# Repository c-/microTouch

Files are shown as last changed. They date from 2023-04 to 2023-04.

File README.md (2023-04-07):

# microTouch

Compact 3D printer bed probe based (very) loosely on the
[TinyTouch NMPG](https://www.thingiverse.com/thing:4661556).

microTouch In Action

I designed and built the first prototype a couple years ago. The current
version has been running since (approximately) May 2022 and has been
quite reliable, with only one misfire that I can remember.

# Design

It uses the same nano servo and a gravity based deployment as the
TT NMPG just started as a project to build a smaller TT PCB, but I've
changed it up to use a hall effect sensor with a small magnet embedded
in the slider, which allows for an even more compact package. I've also
changed the connector to a PH 2.0 and removed the servo connector
completely, soldering it directly to the PCB.

The size of the PCB is approximately 35mm x 25mm, and the shell will add
another 10mm or so. It should comfortably fit in the space needed by
a BLTouch.

I think there's room to crunch the design down even smaller, but I'm not
sure there's any need for a nanoTouch.

# Bill Of Materials

There's an [Interactive BOM](bom/ibom.html) for the electronics.

 * Nano linear servo (RH only). In theory you could use a LH version, but you'd
need to flip the mirror *everything*, including the hall sensor and magnet.
I haven't tested that.
 * A3144 hall effect sensor. This is an obsolete part, but it's still
available.
 * JST PH 2.0 connector. You can use a four or five pin, depending on
whether you need a different voltage for the signal than what the servo
uses (i.e. servo is 5V, signal might be 3.3V). If you use the 5 pin version
then you'll need to cut the solder jumper on the back.
 * 10uF, 100nF 0805 capacitors
 * 4.7K 0805 resistors
 * 0805 red LED (other colors probably work, but I've only tested red)
 * 3x2mm rare earth magnet

You'll need a PCB. It *can* be homemade (I made the first version on a PCB
mill), but you'll have a battle with the servo pads. I ordered my finished
versions [from Oshpark](https://oshpark.com/shared_projects/54oETibN),
and you can't really beat the price for something that small.

You'll need printed parts. Minimally the slider and the cover, and I found
a backer/spacer necessary, but you might need to design a different way to
mount to your printer.  I printed the slider with
[Igus iglide I150-PF](https://www.igus.com/product/12404),
but probably anything would work okay. The slider and the body need to be
sanded to ensure smooth deployment, and getting that right is by far the
most finicky part of the job. You'll probably have to drill the slider hole
larger to hold the magnet (a press fit is enough).

For the probe itself I use a M3 bolt (25mm, I think?), but anything you can
thread into the slider body should be fine as long as it has some weight to
it. The bolt can be threaded in quite far and is the main way to adjust
the position of the problem, along with the servo angles.

# Assembly

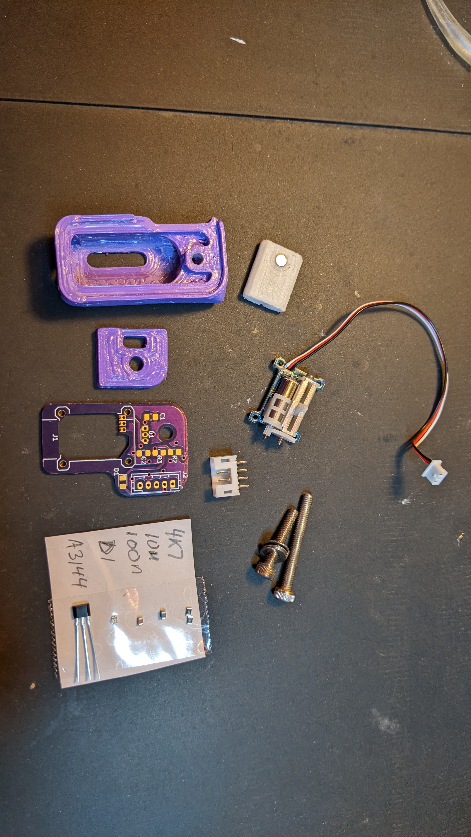
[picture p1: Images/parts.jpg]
All the parts


Remove the wires from the servo.

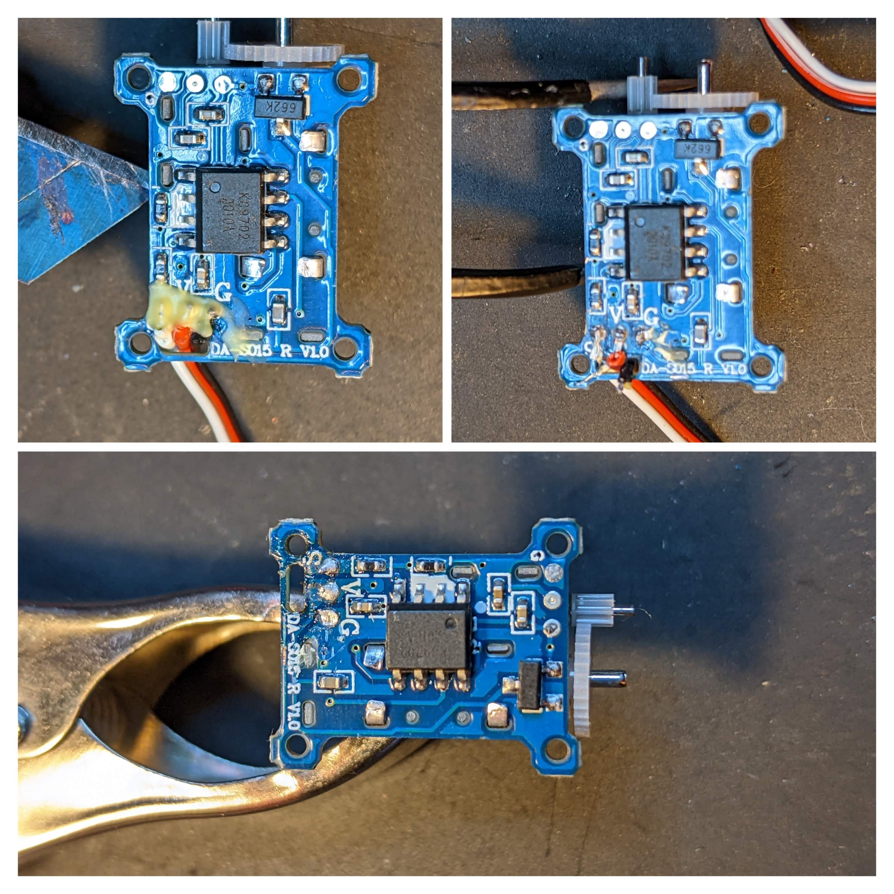
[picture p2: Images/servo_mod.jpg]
Servo wirectomy


Do this by scraping away the glue at the PCB, then desolder the wires and
touch up the pads with fresh solder. Don't overbuild solder on the pads,
they should be somewhat flat.

Solder the components. See the Interactive bom for details of what goes
where. Do the surface mount components first or you'll find things get
cramped. The hall sensor should be mounted a bit off the board, just below
where the slider will clear it.

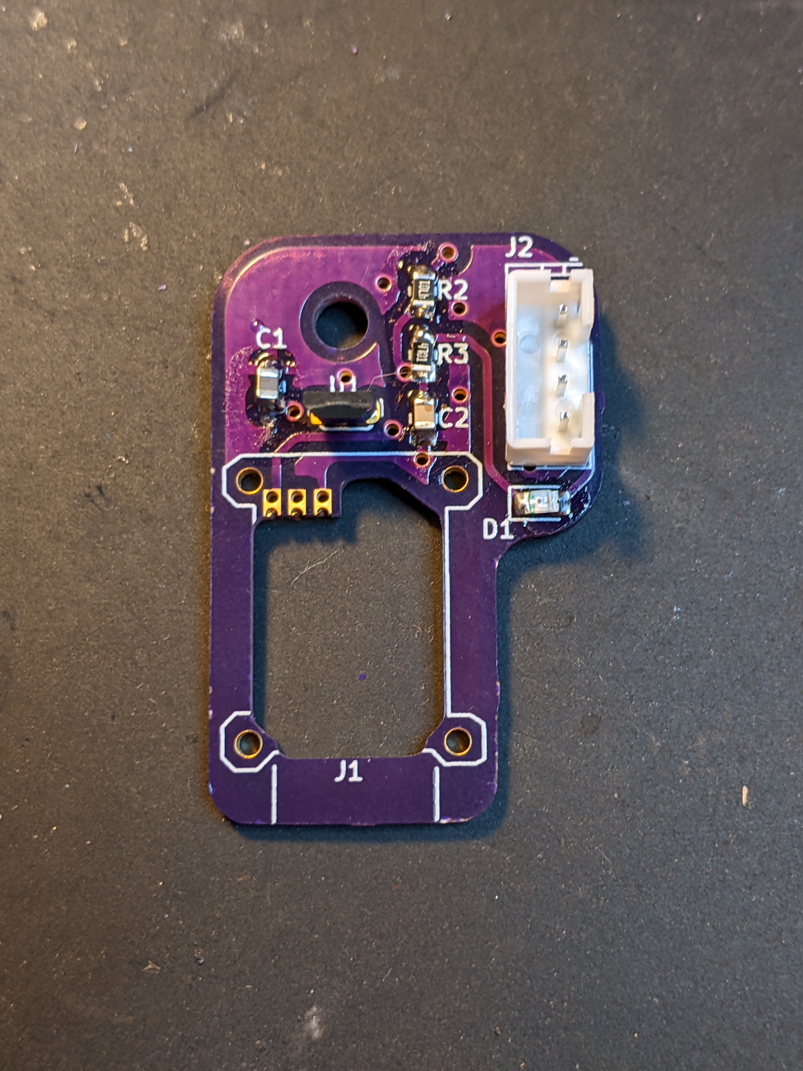
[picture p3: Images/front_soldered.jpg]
Front


Back

Attach the servo.

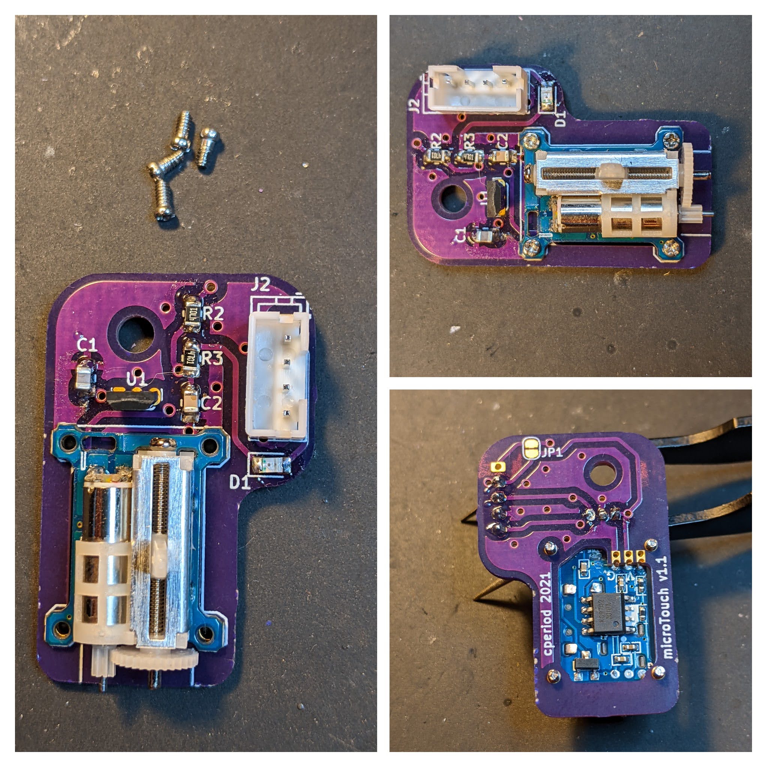
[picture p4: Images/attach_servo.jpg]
Attach the servo


I used tiny eyeglass screws (I want to say 1mm) without bothering to thread
anything. At the back, the wire pads on the servo should align
with the three
[castellated pads](https://docs.oshpark.com/tips+tricks/castellation/).

Solder the servo pads to the castellanations. This is done by stabbing the
iron tip down so it's touching both the pad and the side of the
catellanation, and wicking solder from the top. A fine tip and small
diameter solder would be good for this, and you don't need much solder.

Soldered Servo

With the PCB done, it's time to assemble everything else. It's not a bad
idea to thread the mounting hole for M3 now, but it's probably not
necessary.  Insert the
slider, screw in the plunger, and the PCB should just press in from the
back.

Mechanical Assembly

This would be a good time to run a test before installing it. I use an
Arduino Nano (there's a test script) to run it through its paces. In
particular, you might have to flip the magnet and give the hall sensor a
slight bend in one direction or another. Take note of the deploy/stow
angles for your firmware configuration.

Then attach it to your printer. Mine is attached through a hole in the back
of my X carriage.

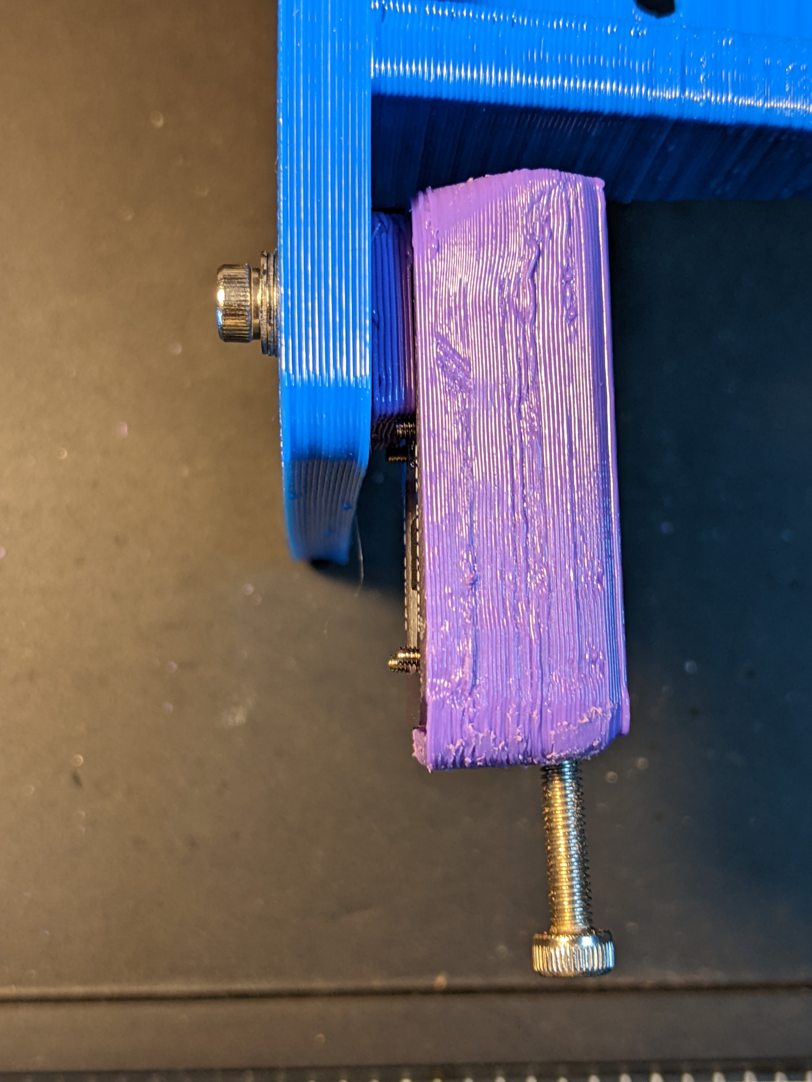
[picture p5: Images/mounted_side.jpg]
Side Mounted


Front Mounted

In hindsight, I probably could have put the connector on the other side.

# Configuration

At the configuration level, it's just your average servo-based probe.
Depending on your servo, polishing, and assembly you *might* not be
able to use the full 180 degree range of the servo due to binding,
but you can still easily achieve a 5mm range between stowed and deployed.

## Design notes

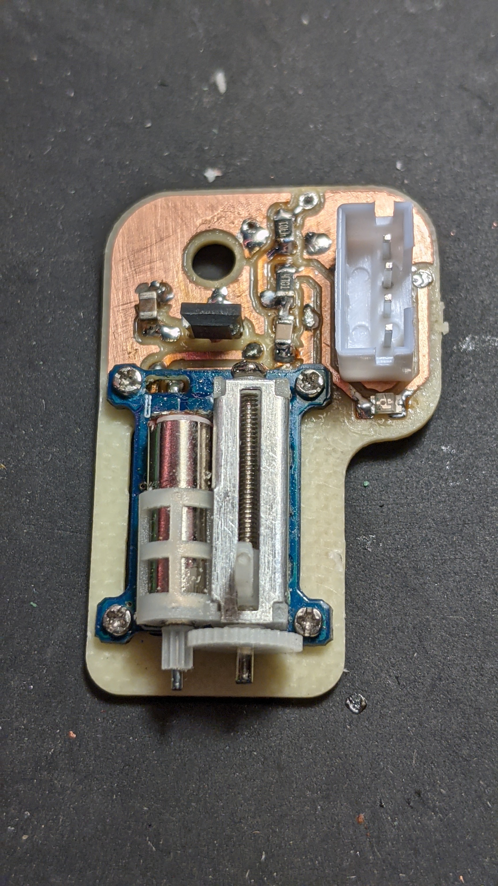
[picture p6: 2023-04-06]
Images/first_version.jpg

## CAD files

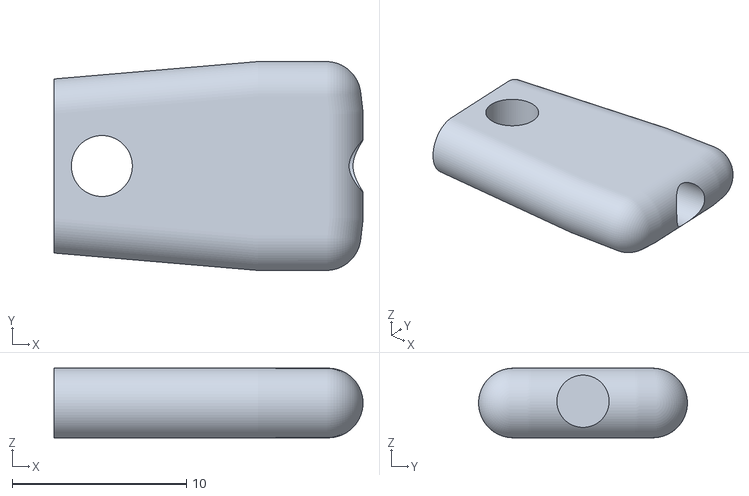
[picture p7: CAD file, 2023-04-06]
Models/microTouch - slider.stl
17.7 x 12.0 x 4.00

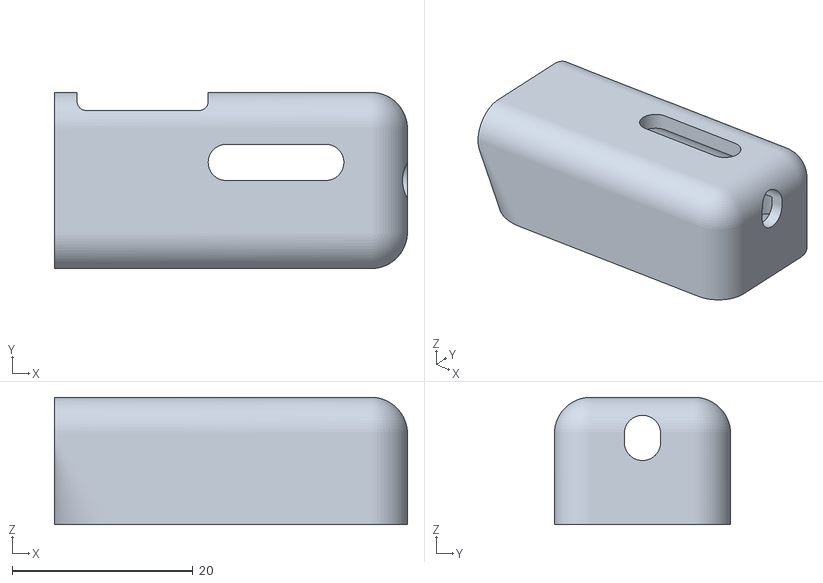
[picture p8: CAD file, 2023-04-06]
Models/microTouch - cover.stl
39.0 x 19.5 x 14.1

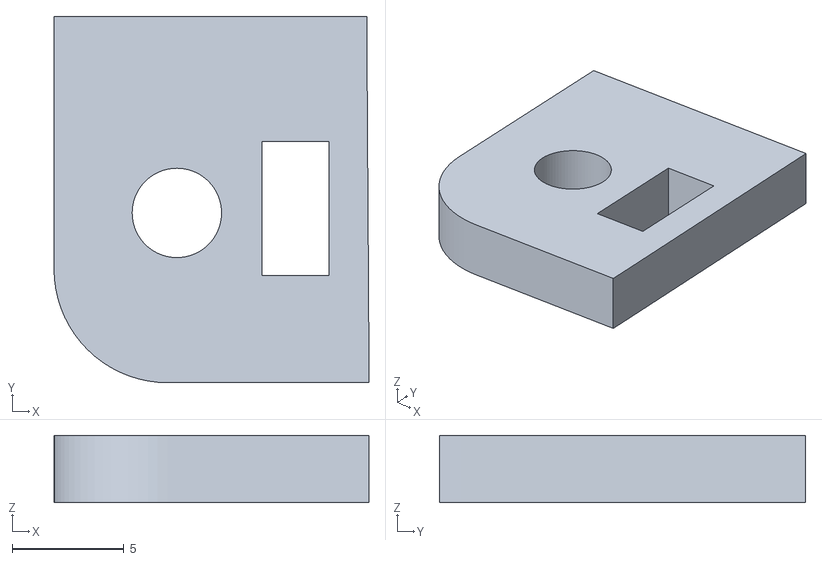
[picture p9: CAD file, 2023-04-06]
Models/microTouch - backer.stl
14.1 x 16.4 x 3.00

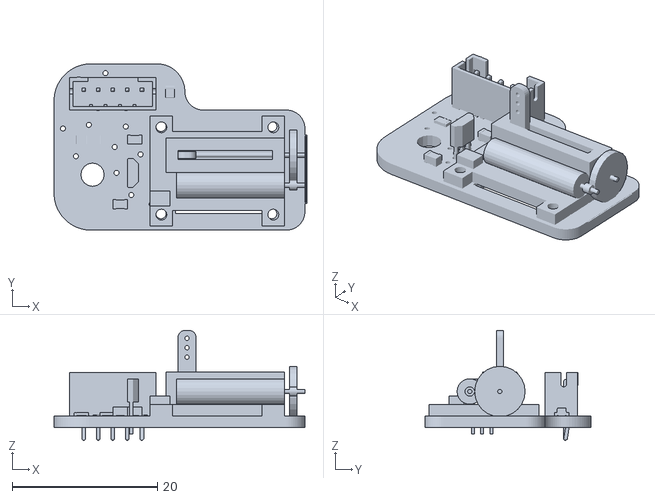
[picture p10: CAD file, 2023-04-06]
Models/microTouch.stl
34.8 x 22.9 x 15.2

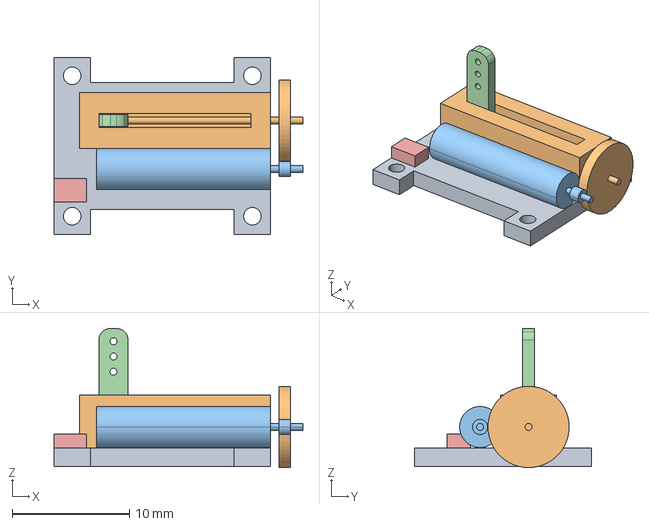
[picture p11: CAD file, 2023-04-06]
Models/micro linear servo.stp
21.3 x 15.1 x 11.9 mm

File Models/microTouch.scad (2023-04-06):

part = "cover";	// [cover, slider, backer]

pcbt = 1.6;
bextra = 0; // pcbt;
t = 1.5;
backert = 3;
pind = 3;
magnetd = 3.5;
magneth = 3;
br = 5.084;	// back corner radius
fr = 2.54;	// front corner radius
tabw = 7;	// bolt tab/spacer width
magnetoffset = 15;
slidelen = magnetoffset + magnetd/2 + 1;
slidew = 12;

// M3 heat set insert for mounting screw, or just M3
// diameter if you want to try threading it directly
insertd = 3;
insertl = 4;

$fn = 72;

module servo() {
	color("teal") import("micro linear servo.stl");
}

module pcb() {
	color("green") translate([-8.254,-20.254,pcbt/2]) import("microTouch.stl");
}


module cylinsphere(r,d,h) {
	r = r ? r : d/2;
	hull() {
		cylinder(r=r,h=0.1);
		translate([0,0,h-r]) sphere(r=r);
	}
}

module slider() {
	w = 2;
	h = 4;
	
	rotate([0,90,0]) difference() {
		union() {
			translate([0.1,0,0]) hull() {
				// taper the body to help prevent binding
				translate([0,-(slidew-h)/2,slidelen*.66])
					cylinsphere(d=h,h=slidelen/3);
				translate([0,(slidew-h)/2,slidelen*.66])
					cylinsphere(d=h,h=slidelen/3);
				translate([0,-(slidew-2-h)/2,0]) cylinsphere(d=h,h=slidelen);
				translate([0,(slidew-2-h)/2,0]) cylinsphere(d=h,h=slidelen);
			}
		}
		
		// pin
		translate([0,0,slidelen/2]) cylinder(d=pind,h=slidelen);
		
		// magnet. making it a through hole means someone can
		// flip it if they screw up polarity
		translate([-h,0,slidelen-magnetoffset])
			rotate([0,90,0]) cylinder(d=magnetd,h=h*2);
	}
}

module rcube(v,cornerr=3,center=false) {
   cr = max(0.1,min(v[0]/2,v[1]/2,cornerr));
	cx = center ? -v[0]/2 : 0;
	cy = center ? -v[1]/2 : 0;
   translate([cr+cx,cr+cy,0]) hull() {
      translate([0,0,0]) cylinder(r=cr,h=v[2]);
      translate([0,v[1]-cr*2,0]) cylinder(r=cr,h=v[2]);
      translate([v[0]-cr*2,0,0]) cylinder(r=cr,h=v[2]);
      translate([v[0]-cr*2,v[1]-cr*2,0])
			cylinder(r=cr,h=v[2]);
   }
}

module backer() {
	difference() {
		hull() {
			translate([br-3.5,br,0]) cylinder(r=br,h=backert);
			translate([-3.5,15.4,0]) cube([14,1,backert]);
			translate([-3.5+14,0,0]) cube([0.1,1,backert]);
		}
		// mounting bolt
		translate([-3.5+5.5, (13+t*2)/2-0.4, -.1])
			cylinder(d=insertd, h=backert*2);
		
		// sensor pins
		translate([5.8,4.8,-.1]) cube([3,6,backert*2]);
	}
}

module cover() {
	bwid = 13.5;
	difference() {
		hull() {
			h = 11;
			
			translate([30,bwid+t*2-fr,-pcbt-bextra])
				cylinsphere(r=fr+t,h=h+t+pcbt+bextra);
			translate([30,fr,-pcbt-bextra])
				cylinsphere(r=fr+t,h=h+t+pcbt+bextra);
			
			translate([br-3.5-t,bwid+t*3-br,-pcbt-bextra])
				cylinsphere(r=br,h=h+t+pcbt+bextra);
			translate([br-3.5,br,-pcbt-bextra])
				cylinsphere(r=br+t,h=h+t+pcbt+bextra);
			
			translate([-3.5-t,fr,h-fr])
				rotate([0,90,0]) cylinder(r=fr+t,h=0.1);
			translate([-3.5-t,bwid+t*2-fr,h-fr])
				rotate([0,90,0]) cylinder(r=fr+t,h=0.1);
		}
		
		// main cutout
		difference() {
			union() {
//				// This needs to go just far enough back to
				// clear the hall sensor
				hull() {
					translate([-t+29,t+(bwid-12)/2,0]) rcube([3,12,0.1],cornerr=3);
					translate([-t+29,t+(bwid-12)/2+1,8]) rcube([3,10,.1],cornerr=3);
					translate([t+9.5,t+bwid/2,0]) cylinder(d1=12,d2=10,h=8);
				}

				// clearance for the passives around the
				// mounting hole
				difference() {
					hull() {
						translate([-t+14,t+(bwid-12)/2,0]) cube([11,12,2.3]);
						translate([t+2-br/2,t-1-br/2+bwid/2,0]) cylinder(d=br,h=2.3);
						translate([t+2-br/2,t+1+br/2+bwid/2,0]) cylinder(d=br,h=2.3);
					}
					
					// want the mounting hole supported flush to the board
					hull() {
						translate([-t, (13+t*2)/2-0.2, -.1])
							cylinder(d=6, h=backert*2);
						translate([2, (13+t*2)/2-0.2, -.1])
							cylinder(d=6, h=backert*2);
					}
				}
			}
		}
		
		// clearance for servo "legs" and fasteners
		translate([0,-0.5,-pcbt-0.1]) hull() {
			translate([9,0,0]) cube([20,17.1,pcbt*2.5]);
			translate([9-2.5,0,0]) cube([22.5,17.1,pcbt]);
		}
		
		// this cutout follows the contour of the PCB. Doesn't need to be
		// perfect, just cutting out a pocket.
		// (FIXME: should just load the PCB as a DXF or something)
		translate([0,0,-pcbt*3+0.1])
		difference() {
			e = 0.5;
			hull() {
				translate([32-3,fr,0]) cylinder(r=fr+e,h=pcbt*3);
				translate([32-3,bwid+t*2-fr,0]) cylinder(r=fr+e,h=pcbt*3);
				translate([br-3.5,bwid+t*2-br+6.4,0])
					cylinder(r=br+e,h=pcbt*3);
				translate([br-3.5+8.4,bwid+t*2-br+6.4,0])
					cylinder(r=br+e,h=pcbt*3);
				translate([br-3.5,br-0.25,0]) cylinder(r=br+e,h=pcbt*3);
			}
			hull() {
				translate([br-3.5+15,bwid+t*2-br+6.5,0])
					cylinder(r=2-e,h=pcbt*3);
				translate([br-3.5+32,bwid+t*2-br+7,0])
					cylinder(r=2,h=pcbt*3);
				translate([br-3.5+15,bwid+t*2-br+12,0])
					cylinder(r=2,h=pcbt*3);
			}
		}

		// extra gear clearance
		translate([28.5+1.5,t+4.5,-pcbt-0.1]) hull() {
			translate([0,-2,10]) mirror([0,0,1]) cylinder(h=10,r=2.5);
			translate([0,10-3,10]) mirror([0,0,1]) cylinder(h=10, r=2.5);
		}
		
		// hole for mounting from the back. This shouldn't go all the way
		// through, since it's nicer to print a bridge
		translate([2, (bwid+t*2)/2-0.4, 0])
			cylinder(d=insertd, h=pcbt+insertl-1);
		
		// front hole
		translate([25,(bwid+t*2)/2,8.5]) rotate([0,90,0])
			hull() {
				cylinder(d=pind+1,h=10);
				translate([1,0,0]) cylinder(d=pind+1,h=10);
			}

		// servo arm clearance and slider viewport
		translate([14,10.25,0]) hull() {
			cylinder(d=4,h=12+t);
			translate([11,0,0]) cylinder(d=4,h=12+t);
		}
		
		// give the connector just a hair of play
		translate([-t-1,16,0]) rcube([14.5,5,15],cornerr=1);
		
		// track for slider. Aside from where the slider is inserted,
		// it's useful for smoothing things with a file.
		translate([-10,(bwid+t*2)/2,7.75]) rotate([0,90,0]) hull() {
			translate([0,-(12-4.5)/2,0]) cylinder(d=5.5,h=38);
			translate([0,(12-4.5)/2,0]) cylinder(d=5.5,h=38);
		}
	}
}

if( part == "slider" ) {
	slider();
} else if( part == "cover" ) {
	cover();
} else if( part == "backer" ) {
	backer();
} else {
	pcb();
   translate([34.8,27.5,pcbt]) servo();
	color("red") translate([-0.75, 15.75, 6+pcbt+2]) slider();
	color("gray")
		translate([10,15.75,pcbt+7.9]) rotate([0,90,0])
			cylinder(d=pind-1,h=25);
	%translate([0,7.7,pcbt]) cover();
	%translate([0,7.7,-backert]) backer();
}

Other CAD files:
Models/micro linear servo.stl

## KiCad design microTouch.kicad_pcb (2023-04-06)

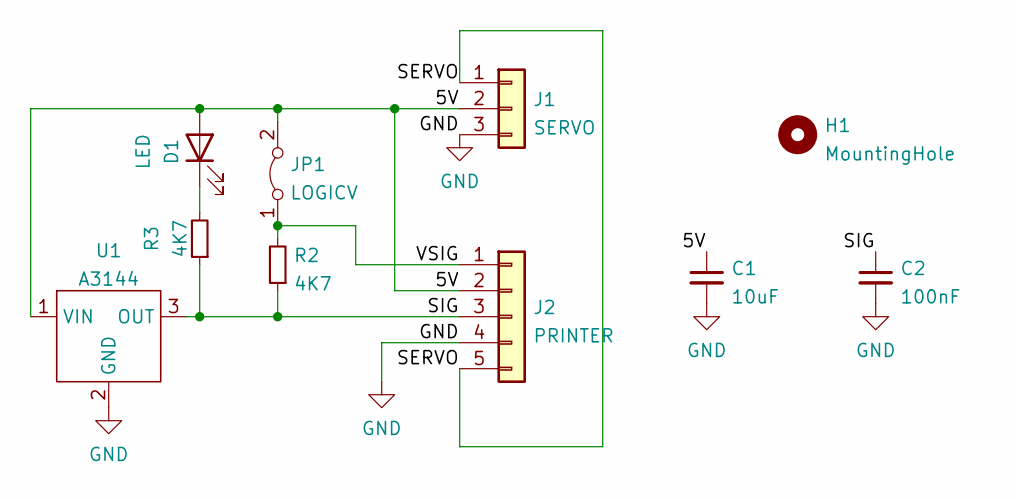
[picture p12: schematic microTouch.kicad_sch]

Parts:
C1: 10uF; C_0805_2012Metric_Pad1.18x1.45mm_HandSolder
C2: 100nF; C_0805_2012Metric_Pad1.18x1.45mm_HandSolder
D1: LED; LED_0805_2012Metric_Pad1.15x1.40mm_HandSolder
H1: MountingHole; MountingHole_3.2mm_M3
J1: SERVO; GS-1502
J2: PRINTER; JST_PH_B5B-PH-K_1x05_P2.00mm_Vertical
JP1: LOGICV; SolderJumper-2_P1.3mm_Bridged_RoundedPad1.0x1.5mm
R2, R3: 4K7; R_0805_2012Metric_Pad1.20x1.40mm_HandSolder
U1: A3144; TO-92Flat

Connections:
/5V: C1.1, D1.2 (A), J1.2, J2.2, JP1.2 (B), U1.1 (VIN)
/SERVO: J1.1, J2.5
/SIG: C2.1, J2.3, R2.1, R3.1, U1.3 (OUT)
/VSIG: J2.1, JP1.1 (A), R2.2
GND: C1.2, C2.2, J1.3, J2.4, U1.2 (GND)
unnamed: D1.1 (K), R3.2

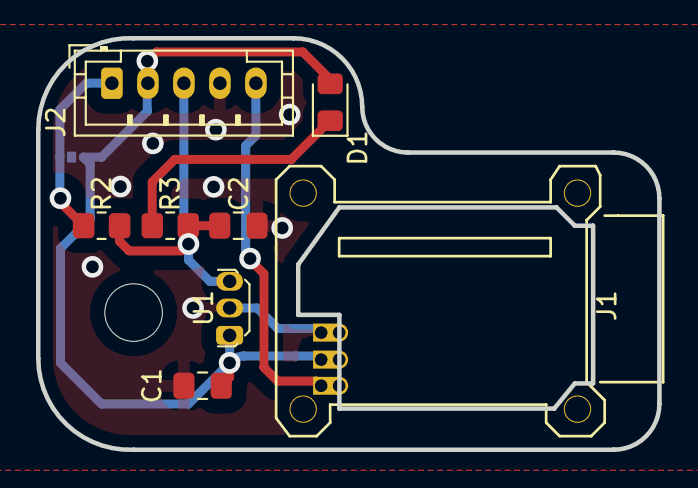
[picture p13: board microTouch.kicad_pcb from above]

Board: 2 copper layers, 34.5 x 22.9 mm, 10 parts (1 on the bottom side), 6 nets.

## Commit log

2023-04-06 PCB first rev
    [microTouch.kicad_pcb, microTouch.kicad_sch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]
2023-04-06 almost there with model
    [micro linear servo.stl, microTouch.scad, microTouch.stl]
2023-04-06 assorted tweaks
    [microTouch.kicad_pcb, microTouch.kicad_sch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]
2023-04-06 more model work
    [microTouch - cover.stl, microTouch - flag.stl, microTouch.scad]
2023-04-06 fix photint pinout, adjust pullup, move LED out further
    [microTouch.kicad_pcb, microTouch.kicad_sch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]
2023-04-06 more tweaking and cleanups
    [microTouch - cover.stl, microTouch.scad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]
2023-04-06 add BOM
2023-04-06 small refinements, but good enough
    [microTouch - cover.stl, microTouch.scad]
2023-04-06 adjust flag for a greater range between stowed and triggered
    [microTouch - flag.stl, microTouch.scad]
2023-04-06 more minor tweaks
    [microTouch - cover.stl, microTouch - flag.stl, microTouch.kicad_pcb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]
2023-04-06 redesign with a A3144 hall effect sensor
    [micro linear servo.stp, microTouch - cover.stl, microTouch - flag.stl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]
2023-04-06 whole bunch of tweaks to match the board, cleanup the layout
    [microTouch - cover.stl, microTouch - slider.stl, microTouch.scad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]
2023-04-06 move some stuff around, add some filter caps for noise
    [microTouch.kicad_pcb, microTouch.kicad_sch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]
2023-04-06 need some kind of backer/spacer plate when mounting to a flat surface
    [microTouch - backer.stl, microTouch.scad]
2023-04-06 thicker backer
    [microTouch - backer.stl, microTouch.scad]
2023-04-06 use a tab for the screw
    [microTouch - cover.stl, microTouch.scad]
2023-04-06 small stuff
    [microTouch.kicad_pcb]
2023-04-06 some adjustments against a real board
    [microTouch - cover.stl, microTouch - slider.stl, microTouch.scad]
2023-04-06 a few more layout tweaks
    [microTouch.kicad_pcb, microTouch.kicad_sch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]
2023-04-06 update BOM
2023-04-06 a few more model tweaks
    [microTouch - cover.stl, microTouch - slider.stl, microTouch.scad]
2023-04-06 redo the track rounding
    [microTouch-rounded.kicad_pcb, microTouch.kicad_pcb]
2023-04-06 fix up the model a bit
    [microTouch - cover.stl, microTouch.scad]
2023-04-06 more cover refinements
    [microTouch - cover.stl, microTouch.scad]
2023-04-06 forgot to label the bins in the silk screen
    [microTouch-rounded.kicad_pcb, microTouch.kicad_pcb]
2023-04-06 more model tweaks
    [microTouch - cover.stl, microTouch - slider.stl, microTouch.scad]
2023-04-07 forgot to mention the magnet
